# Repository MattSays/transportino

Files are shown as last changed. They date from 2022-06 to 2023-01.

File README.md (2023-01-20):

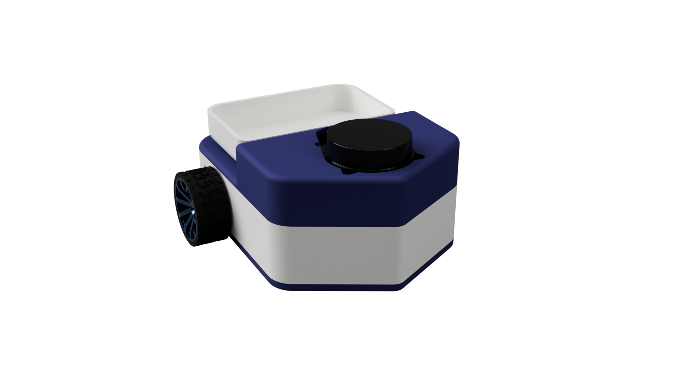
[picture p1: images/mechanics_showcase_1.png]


# transportino

## Overview

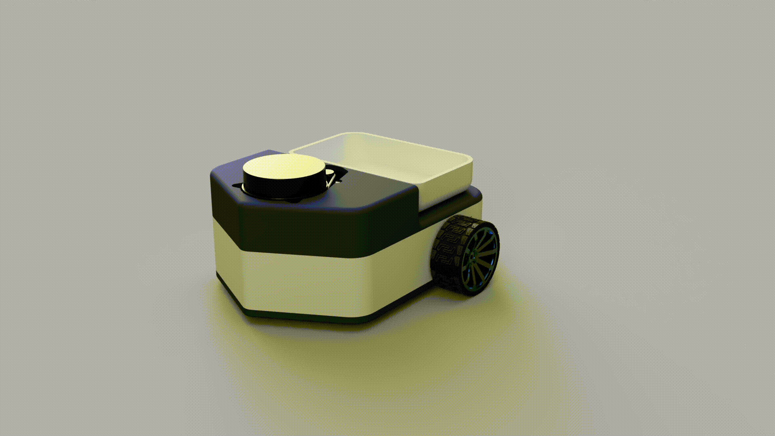
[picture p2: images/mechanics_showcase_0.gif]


## About the project

Transportino is an automated robot that can bring you things around the house using just your vocal assistant.

Making and also understanding this project will hopefully help enthusiasts that want to know more about robotics and automated navigation, learn the basics of it.

However, this project was born because of my curiosity to learn robotics so It is far from industrial perfection. If you have new ideas or you want to change something just make a pull request!

## Why this name?

Its name is literally made of two words: Transport and Arduino. 

## What's the main idea behind it?

This robot was originally meant to be a new version of an older one called [ArduCar](https://github.com/mattsays/arducar).

However it ended up being an entirely new robot that required me to make things entirely different and it was also an opportunity for me to learn more stuff about robotics, electronics, programming and also a little bit of mechanics.

This is just a project that I made to explore a field that was quite unknown to me and that made really passionate about.

So the main idea behind the whole project is making a robot which can move objects from one room of your house to another one.
The robot should know how to navigate in your house and at least bring objects at the entrance of the room.

## Known Limitations

Transportino has a raspberry pi 3 at its core, so by actually making It, I have encountered several performance issues that made me voluntarily limit the wanted capabilities of the robot.
For example, I had to separate the route planning algorithm from the actual robot and make it run on my local computer so I could lower the load on the raspberry.
It also would have been great if I implemented a more efficient cooling system.
Besides these major issues, I can proudly say that making this robot has made me learn a lot about what challenges are encountered when making a robot and I love it.

## What is it made of?

Transportino is composed by three important parts:
- [Mechanics](https://github.com/mattsays/transportino/tree/main/mechanics), the main structure, the usage of the right motors for a specific torque, etc.
- [Electronics](https://github.com/mattsays/transportino/tree/main/electronics), the main motherboard, data connections with raspberry pi and power management.
- [Software](https://github.com/mattsays/transportino/tree/main/code), the ros2 application that controls all the motors and analyzes data appropriately.

## To Do list

- [X] Make the main motherboard
- [X] Code the embedded part
- [X] Add ROS2 integration
- [X] Make a decent design that so Transportino looks sexy.
- [ ] Add integration with Amazon Alexa.
- [ ] Add a speaker so Transportino can also talk.
- [X] Add some cool aesthetics.

## Some cool renderings and animations 

transportino
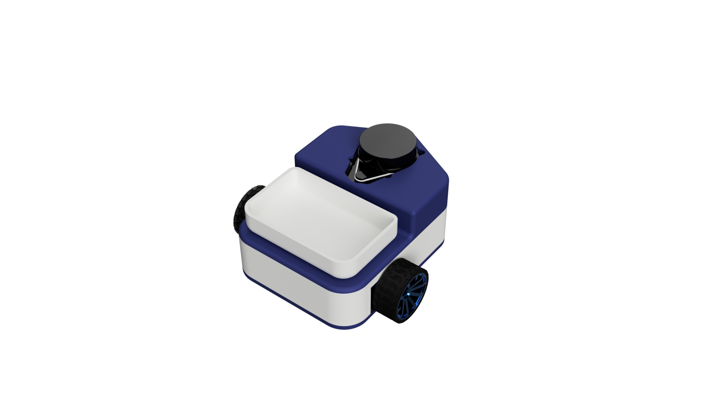
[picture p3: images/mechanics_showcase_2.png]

transportino

## What is that 46 logo?

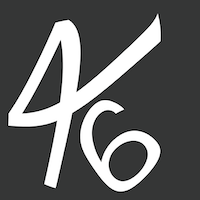
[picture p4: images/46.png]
fortisix


This logo it literally has no sense, it is from a startup idea named "Fortisix" that I had some time ago which had this beautiful and simple logo.

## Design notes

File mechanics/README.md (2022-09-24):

# Mechanics

The main structure of Transportino has been made with Fusion360.

The mechanical part has required me some time to not only make minimal functional unit but also to make it printable on my Ender 3 with BL Touch (They can be found on "print_files" folder).

It is essentially made of 3 main parts:
- Back part which contains the **motors** and the **battery**.
- Front part which contains a **raspberry pi** (3B+ in my case but you could use a 4) and the [**main motherboard**](https://github.com/Transportino/transportino/tree/main/electronics)
- Top part which contains the [**Lidar**](https://www.aliexpress.com/item/4001253880158.html?spm=a2g0o.order_list.0.0.21ef1802iWpH9n) and the **container** with a bowl-like shape.

> Those parts have been splitted further to make it printable within the max sizes of my 3d printer, 
so there are some connectors that are not really good right now but will be improved later (*My current main objective is to make the robot functional*).

Structurally It is three wheeled robot with two motors and one caster wheel.

Another important topic is choosing the right motors for my needs.

I decided to go with this two motors from [AliExpress](https://www.aliexpress.com/item/4001339371886.html?spm=a2g0o.order_list.0.0.21ef1802iWpH9n).

Considering that each of my motors have a torque of 6.5 kg • cm (A total of 13 kg • cm torque).
Transportino could theoretically handle up to 2.8 kg (Considering that Transportino weight is around 1 kg).

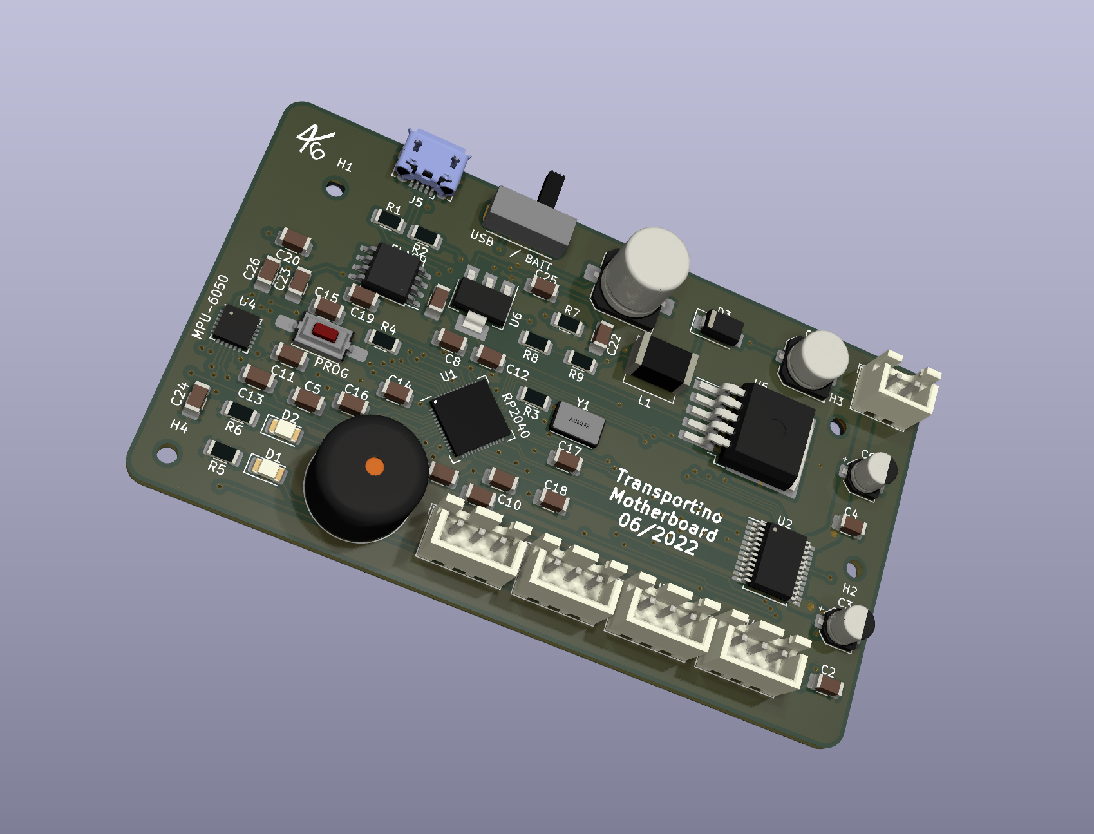
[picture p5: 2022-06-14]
images/pcb_1.png

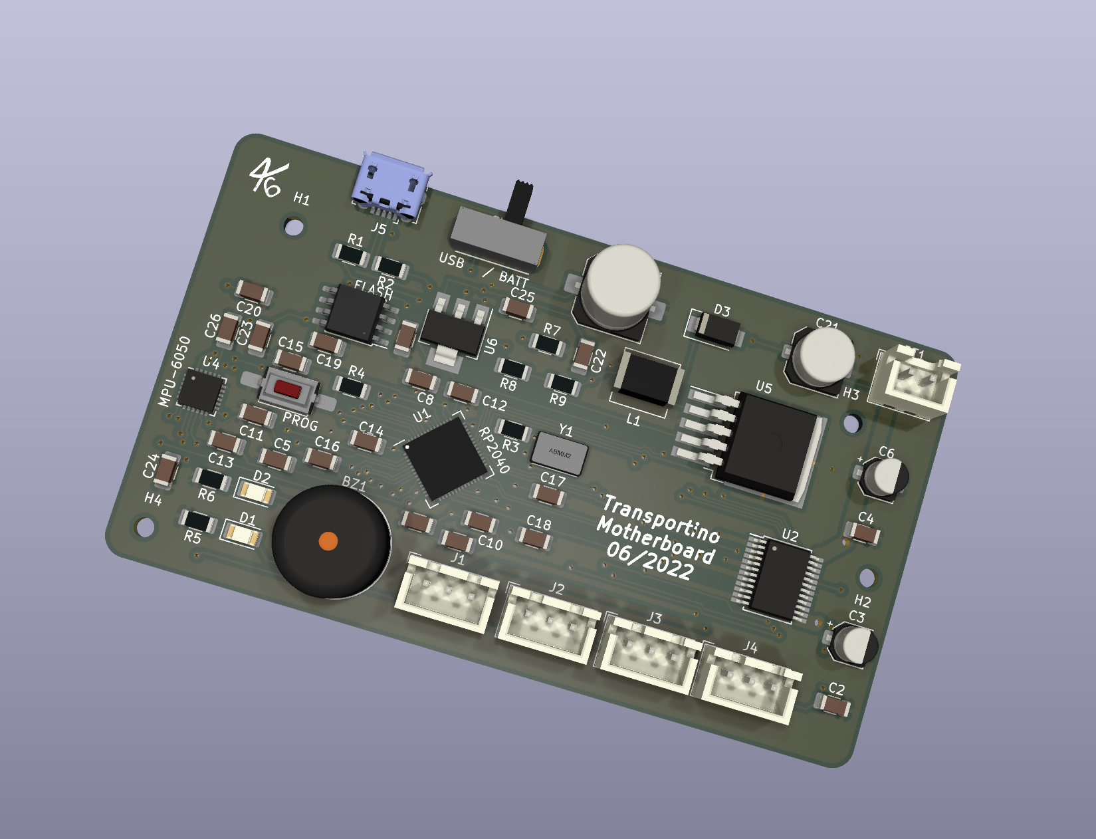
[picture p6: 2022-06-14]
images/pcb_2.png

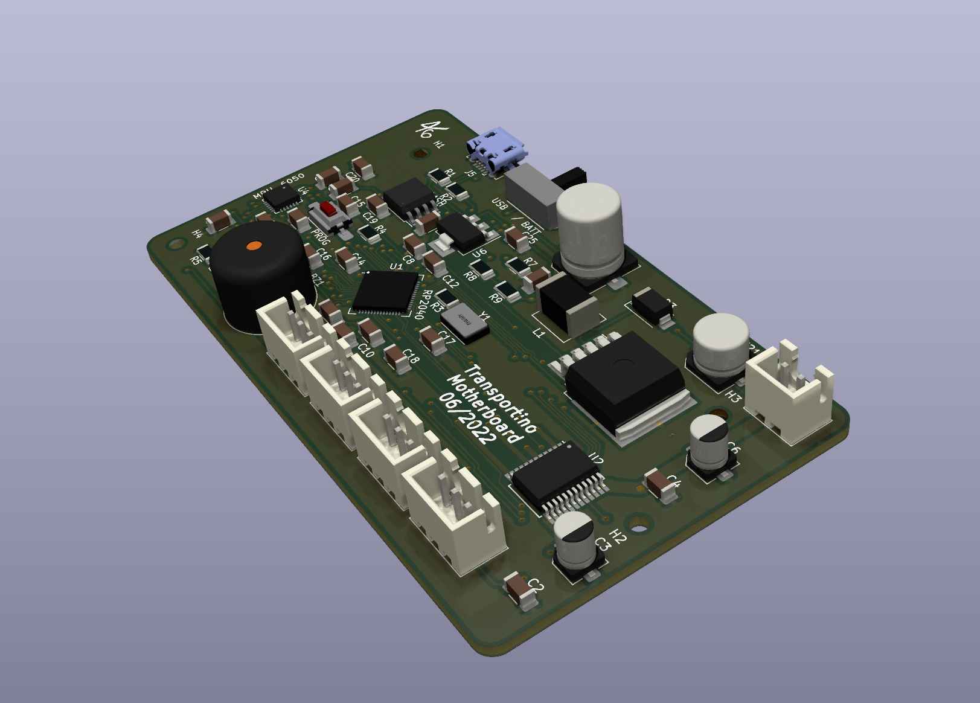
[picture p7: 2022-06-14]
images/pcb_0.png

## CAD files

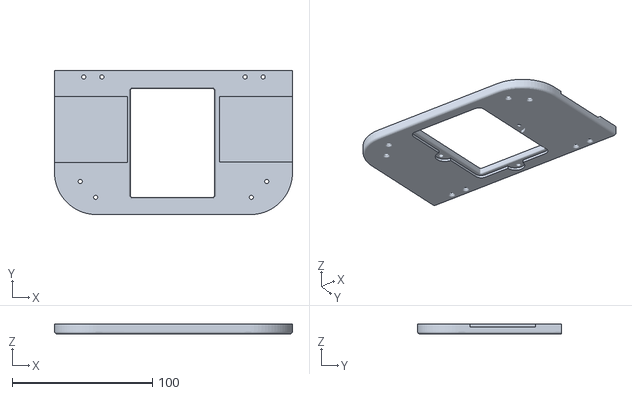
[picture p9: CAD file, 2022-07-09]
mechanics/print_files/ender3/bottom_0.stl
170.0 x 103.0 x 7.00

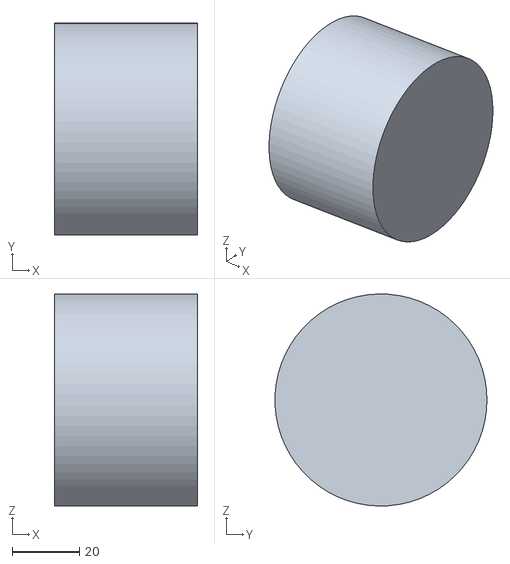
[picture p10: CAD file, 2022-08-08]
mechanics/urdf_meshes/wheel_left_link.stl
42.6 x 63.0 x 63.0

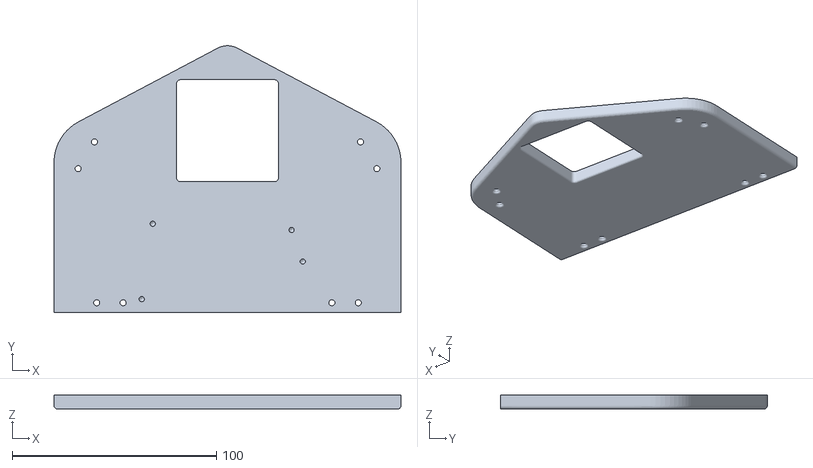
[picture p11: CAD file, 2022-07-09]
mechanics/print_files/ender3/bottom_1.stl
170.0 x 130.7 x 7.00

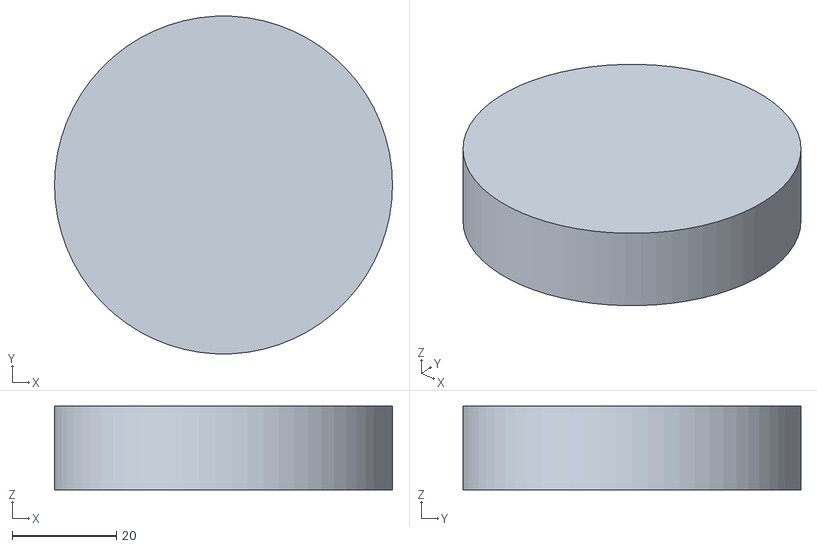
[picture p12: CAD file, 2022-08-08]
mechanics/urdf_meshes/laser_link.stl
64.7 x 64.7 x 16.0

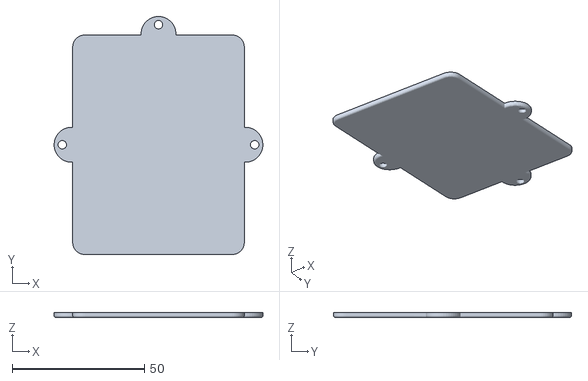
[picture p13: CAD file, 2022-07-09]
mechanics/print_files/ender3/battery_cover.stl
78.9 x 89.9 x 2.00

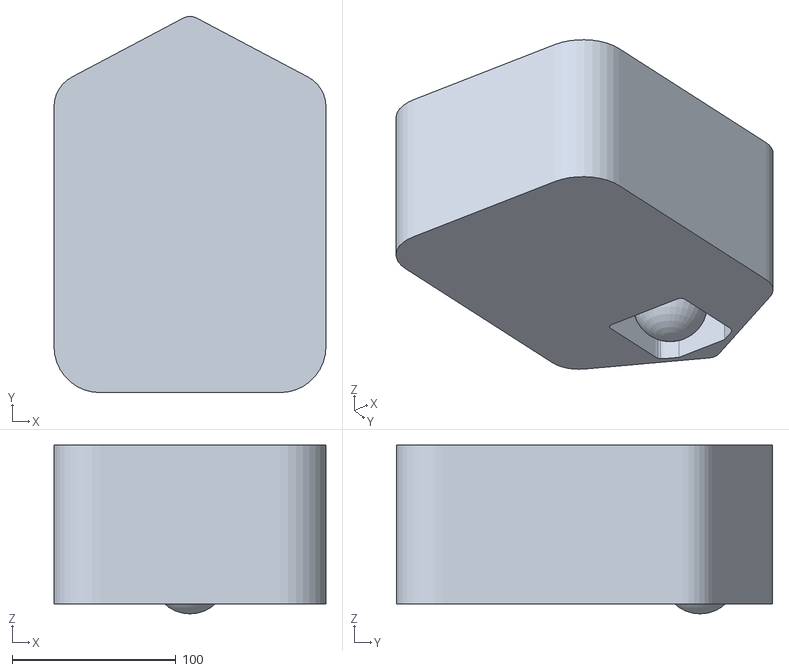
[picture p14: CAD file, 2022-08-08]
mechanics/urdf_meshes/base_link.stl
166.0 x 229.6 x 103.0

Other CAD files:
mechanics/urdf_meshes/wheel_right_link.stl

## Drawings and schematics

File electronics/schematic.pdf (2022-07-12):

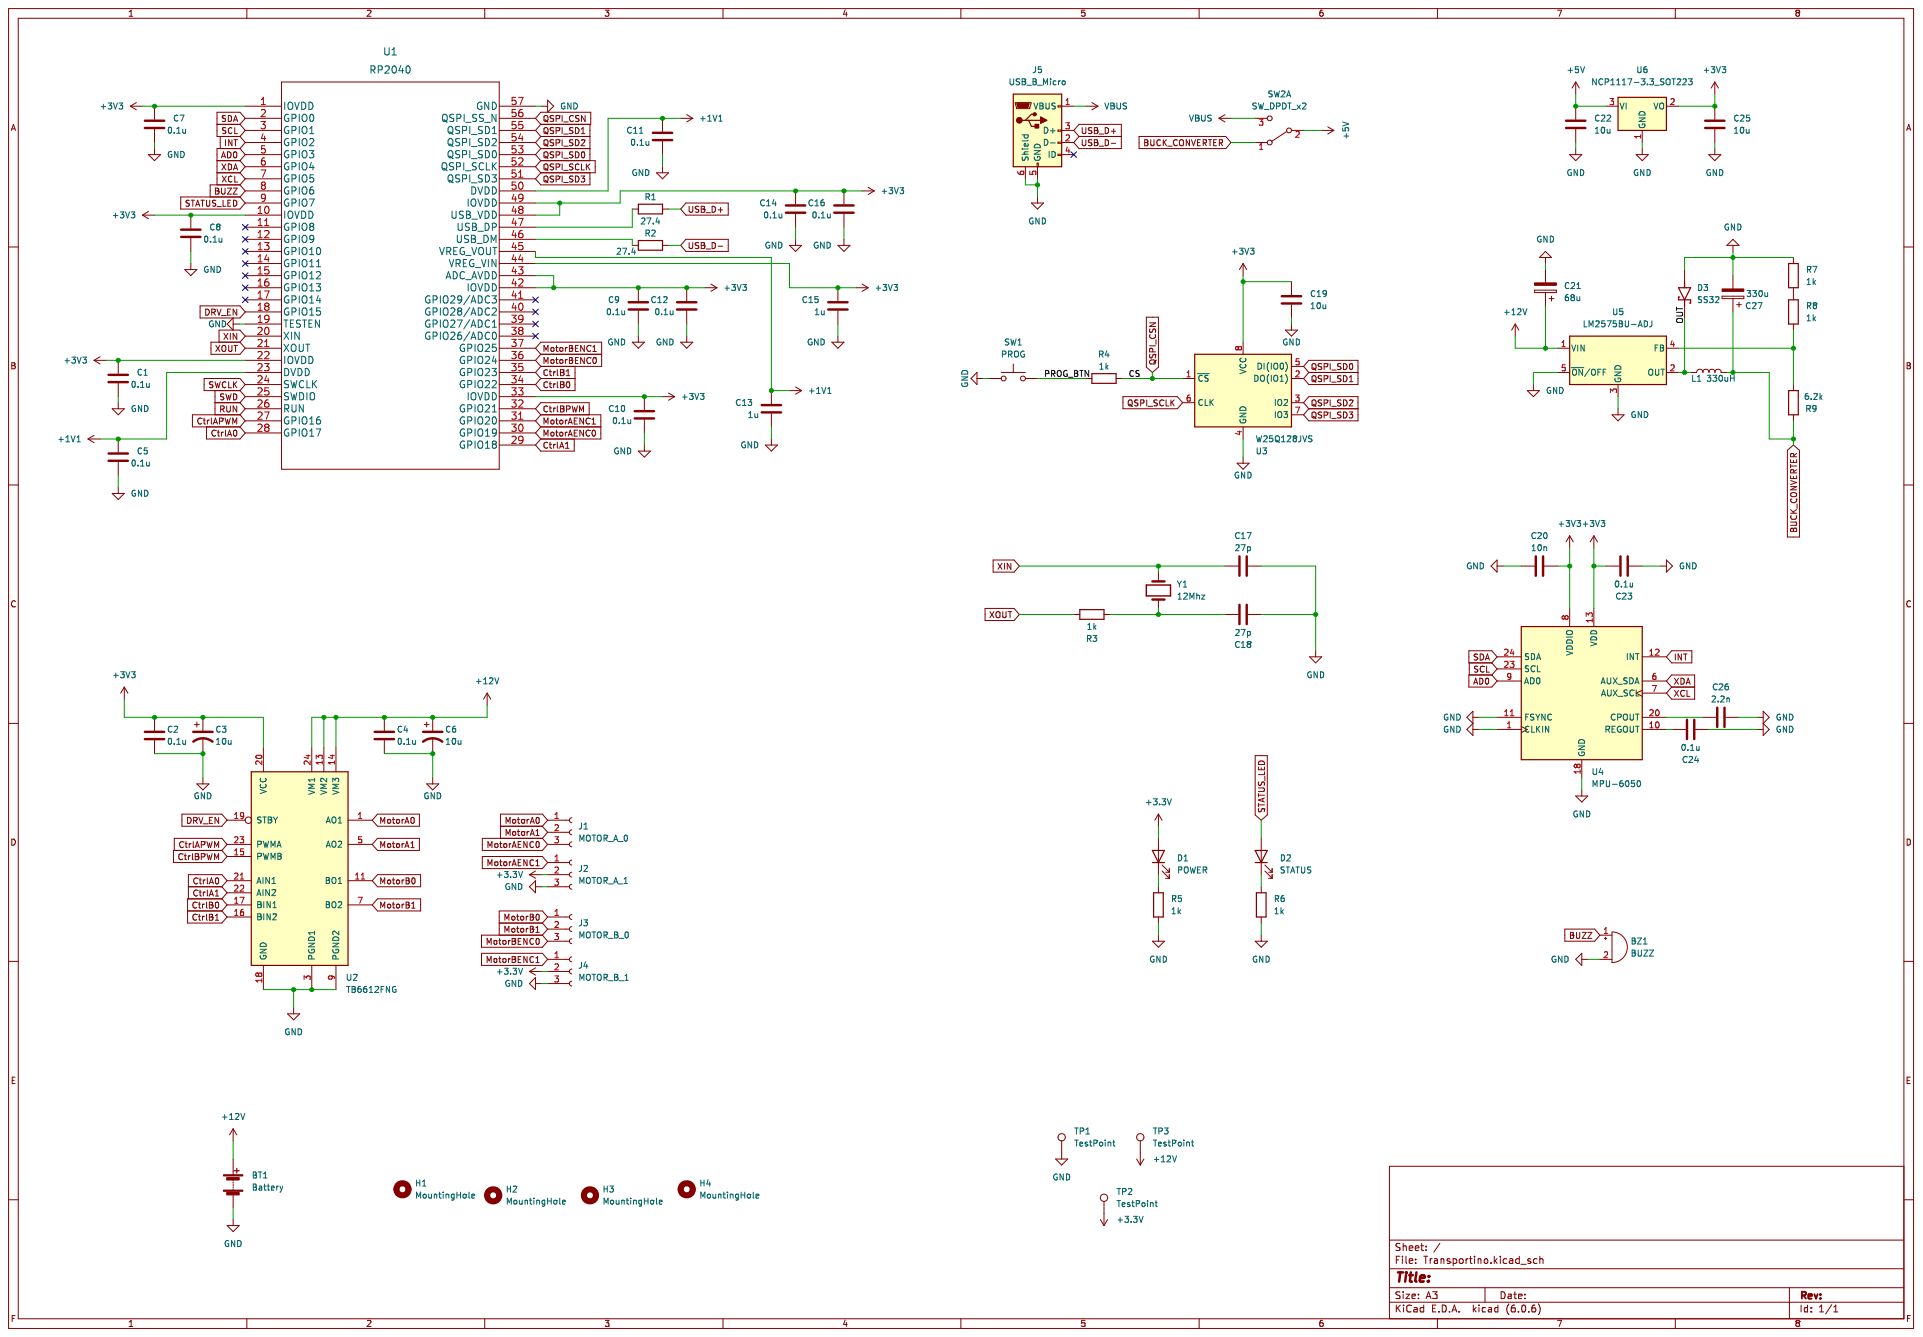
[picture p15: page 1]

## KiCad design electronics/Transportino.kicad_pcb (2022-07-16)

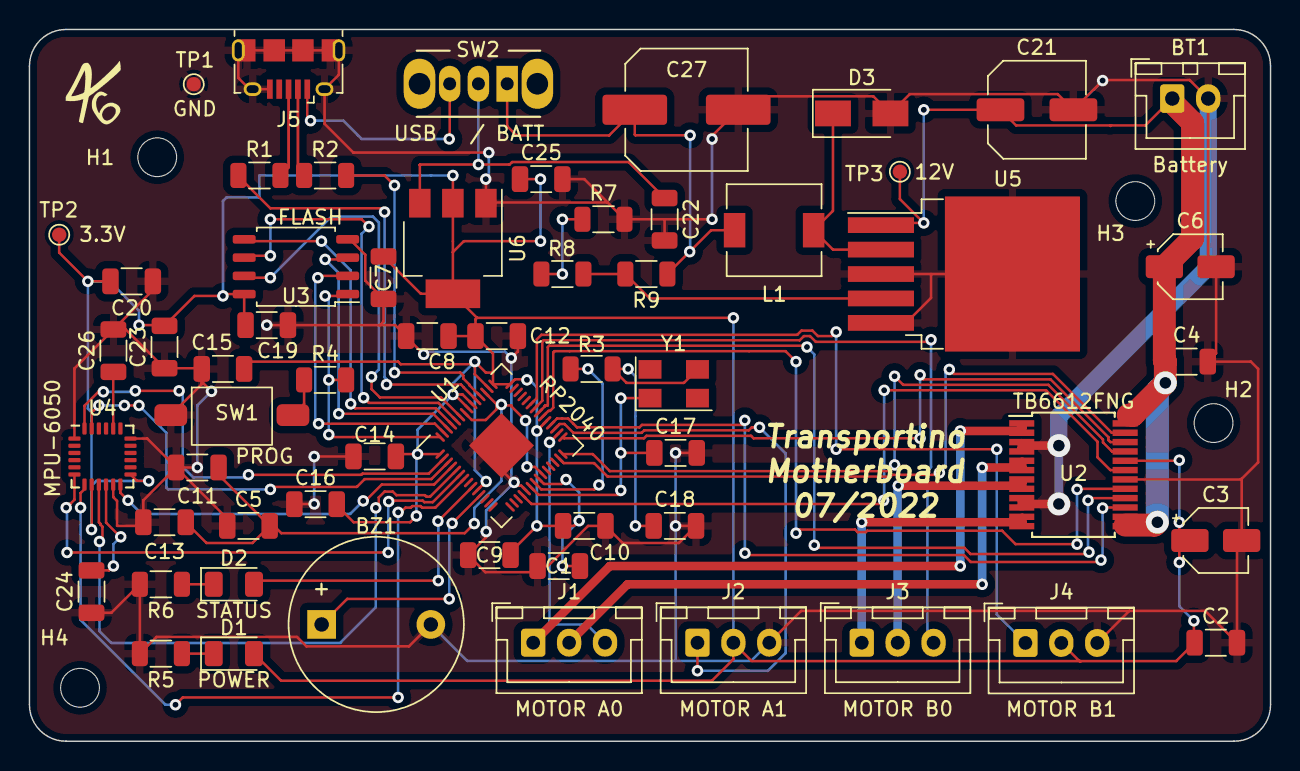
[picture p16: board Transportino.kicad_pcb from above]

Board: 2 copper layers, 86.4 x 49.5 mm, 63 parts (0 on the bottom side), 51 nets.

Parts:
BT1: Battery; JST_XH_B2B-XH-A_1x02_P2.50mm_Vertical
BZ1: BUZZ; Buzzer_12x9.5RM7.6
C1, C2, C4, C5, C7, C8, C9, C10, C11, C12, C14, C16, C23, C24: 0.1u; C_1206_3216Metric
C3, C6: 10u; CP_Elec_4x5.4
C13, C15: 1u; C_1206_3216Metric
C17, C18: 27p; C_1206_3216Metric
C19, C22, C25: 10u; C_1206_3216Metric
C20: 10n; C_1206_3216Metric
C21: 68u; C_Elec_6.3x5.4
C26: 2.2n; C_1206_3216Metric
C27: 330u; C_Elec_8x10.2
D1: POWER; LED_1206_3216Metric
D2: STATUS; LED_1206_3216Metric
D3: SS32; D_SMA
H1, H2, H3, H4: MountingHole; MountingHole_2.7mm_M2.5
J1: MOTOR A0; JST_XH_B3B-XH-A_1x03_P2.50mm_Vertical
J2: MOTOR A1; JST_XH_B3B-XH-A_1x03_P2.50mm_Vertical
J3: MOTOR B0; JST_XH_B3B-XH-A_1x03_P2.50mm_Vertical
J4: MOTOR B1; JST_XH_B3B-XH-A_1x03_P2.50mm_Vertical
J5: USB_B_Micro; USB_Micro-B_Amphenol_10118194_Horizontal
L1: 330uH; L_6.3x6.3_H3
R1, R2: 27.4; R_1206_3216Metric
R3, R4, R5, R6, R7, R8: 1k; R_1206_3216Metric
R9: 6.2k; R_1206_3216Metric
SW1: PROG; Button_SWITCH_6.1x3.7
SW2: SW_DPDT_x2; SW_CuK_OS102011MA1QN1_SPDT_Angled
TP1: TestPoint; TestPoint_Pad_D1.0mm
TP2: 3.3V; TestPoint_Pad_D1.0mm
TP3: 12V; TestPoint_Pad_D1.0mm
U1: RP2040; QFN-56_EP_7.75x7.75_Pitch0.4mm
U2: TB6612FNG; SSOP-24_5.3x8.2mm_P0.65mm
U3: FLASH; SOIC-8_5.23x5.23mm_P1.27mm
U4: MPU-6050; InvenSense_QFN-24_4x4mm_P0.5mm
U5: LM2575BU-ADJ; TO-263-5_TabPin3
U6: NCP1117-3.3_SOT223; SOT-223-3_TabPin2
Y1: 12Mhz; Crystal_SMD_5032-4Pin_5.0x3.2mm

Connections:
+1V1: C5.2, C11.2, C13.2, U1.23 (DVDD), U1.45 (VREG_VOUT), U1.50 (DVDD)
+3V3: C1.2, C2.1, C3.1, C7.2, C8.2, C9.2, C10.2, C12.2, C14.2, C15.2, C16.2, C19.1, C20.2, C23.2, C25.1, D1.2 (A), J2.2, J4.2, TP2.1, U1.1 (IOVDD), U1.10 (IOVDD), U1.22 (IOVDD), U1.33 (IOVDD), U1.42 (IOVDD), U1.43 (ADC_AVDD), U1.44 (VREG_VIN), U1.48 (USB_VDD), U1.49 (IOVDD), U2.20 (VCC), U3.8 (VCC), U4.8 (VDDIO), U4.13 (VDD), U6.2 (VO)
+5V: C22.1, SW2.2 (B), U6.3 (VI)
+12V: BT1.1 (+), C4.1, C6.1, C21.1, TP3.1, U2.13 (VM2), U2.14 (VM3), U2.24 (VM1), U5.1 (VIN)
/OUT: D3.1, L1.1, U5.2 (OUT)
/PROG_BTN: R4.1, SW1.2
AD0: U1.5 (GPIO3), U4.9 (AD0)
BUCK_CONVERTER: C27.1, L1.2, R9.1, SW2.1 (A)
BUZZ: BZ1.1 (-), U1.11 (GPIO8)
CtrlA0: U1.28 (GPIO17), U2.21 (AIN1)
CtrlA1: U1.29 (GPIO18), U2.22 (AIN2)
CtrlAPWM: U1.27 (GPIO16), U2.23 (PWMA)
CtrlB0: U1.34 (GPIO22), U2.17 (BIN1)
CtrlB1: U1.35 (GPIO23), U2.16 (BIN2)
CtrlBPWM: U1.32 (GPIO21), U2.15 (PWMB)
DRV_EN: U1.18 (GPIO15), U2.19 (STBY)
GND: BT1.2 (-), BZ1.2 (+), C1.1, C2.2, C3.2, C4.2, C5.1, C6.2, C7.1, C8.1, C9.1, C10.1, C11.1, C12.1, C13.1, C14.1, C15.1, C16.1, C17.2, C18.2, C19.2, C20.1, C21.2, C22.2, C23.1, C24.1, C25.2, C26.2, C27.2, D3.2, J2.3, J4.3, J5.5 (GND), J5.6 (Shield), R5.2, R6.2, R7.2, SW1.1, TP1.1, U1.19 (TESTEN), U1.57 (GND), U2.3 (PGND1), U2.4 (PGND1), U2.9 (PGND2), U2.10 (PGND2), U2.18 (GND), U3.4 (GND), U4.1 (CLKIN), U4.11 (FSYNC), U4.18 (GND), U5.3 (GND), U5.5 (~ON/OFF), U6.1 (GND)
INT: U1.4 (GPIO2), U4.12 (INT)
MotorA0: J1.1, U2.1 (AO1), U2.2 (AO1)
MotorA1: J1.2, U2.5 (AO2), U2.6 (AO2)
MotorAENC0: J1.3, U1.30 (GPIO19)
MotorAENC1: J2.1, U1.31 (GPIO20)
MotorB0: J3.1, U2.11 (BO1), U2.12 (BO1)
MotorB1: J3.2, U2.7 (BO2), U2.8 (BO2)
MotorBENC0: J3.3, U1.36 (GPIO24)
MotorBENC1: J4.1, U1.37 (GPIO25)
unnamed: C18.1, R3.1, Y1.3
unnamed: C24.2, U4.10 (REGOUT)
unnamed: C26.1, U4.20 (CPOUT)
unnamed: D1.1 (K), R5.1
unnamed: D2.1 (K), R6.1
unnamed: R1.1, U1.47 (USB_DP)
unnamed: R2.1, U1.46 (USB_DM)
unnamed: R7.1, R8.2
unnamed: R8.1, R9.2, U5.4 (FB)
QSPI_CSN: R4.2, U1.56 (QSPI_SS_N), U3.1 (~CS)
QSPI_SCLK: U1.52 (QSPI_SCLK), U3.6 (CLK)
QSPI_SD0: U1.53 (QSPI_SD0), U3.5 (DI(IO0))
QSPI_SD1: U1.55 (QSPI_SD1), U3.2 (DO(IO1))
QSPI_SD2: U1.54 (QSPI_SD2), U3.3 (IO2)
QSPI_SD3: U1.51 (QSPI_SD3), U3.7 (IO3)
SCL: U1.3 (GPIO1), U4.23 (SCL)
SDA: U1.2 (GPIO0), U4.24 (SDA)
STATUS_LED: D2.2 (A), U1.9 (GPIO7)
USB_D+: J5.3 (D+), R1.2
USB_D-: J5.2 (D-), R2.2
VBUS: J5.1 (VBUS), SW2.3 (C)
XCL: U1.7 (GPIO5), U4.7 (AUX_SCL)
XDA: U1.6 (GPIO4), U4.6 (AUX_SDA)
XIN: C17.1, U1.20 (XIN), Y1.1
XOUT: R3.2, U1.21 (XOUT)

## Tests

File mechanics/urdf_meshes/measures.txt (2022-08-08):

base_link __ x = 166.00mm, y = 229.685mm, z = 97.00mm
base_link -> wheel_left_link = (-104.293mm, -32.307mm, 25.006mm) } __ radius = 33.5mm, height = 42.587mm
base_link -> wheel_right_link = (104.393mm, -32.307mm, 25.006mm) } 
base_link -> laser_link = (0.000mm, 80.404mm, 105.00mm) __ radius = 32.368mm, height = 16.00mm
base_link -> imu_link = (-2.36mm, 27.318mm, 7.0mm)

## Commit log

2022-06-04 Removed MPU6050 symbol
    [Transportino.kicad_sch]
2022-06-04 Rearranged components
    [Transportino.kicad_sch]
2022-06-13 Changed components and added new ones
    [Transportino-B_Cu.gbr, Transportino-B_Mask.gbr, Transportino-B_Paste.gbr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]
2022-06-15 Improved readme.md and added holes to mainboard
    [Transportino-B_Cu.gbr, Transportino-B_Mask.gbr, Transportino-B_Paste.gbr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]
2022-06-16 Added link to the ArduCar repo
    [Transportino.kicad_pcb, Transportino.kicad_sch]
2022-06-21 Added mechanics part and some renderings.
    [Transportino.kicad_pcb]
2022-07-09 Added ros part
    [Transportino.kicad_pcb, Transportino.kicad_sch, battery_cover.stl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]
2022-07-11 Added html bom
2022-07-11 Added html bom and modified gitignore
2022-07-13 Changed wrong assigned crystal pin.
    [Transportino.kicad_pcb]
2022-07-16 Changed buzzer gpio pin.
    [Transportino.kicad_pcb, Transportino.kicad_sch]
2022-07-22 Added board firmware
2022-08-08 Added urdf meshes and updated fusion file
    [base_link.stl, laser_link.stl, wheel_left_link.stl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]
